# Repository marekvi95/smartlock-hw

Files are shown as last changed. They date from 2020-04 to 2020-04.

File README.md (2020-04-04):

# smartlock-hw

This repository contains PCB design for the **smartlock**. This project started as the final thesis at the Brno University of Technology. The aim of this project is to create a smartlock that that could be used for securing the objects.

Project is created with KiCAD version 6.0.0 nightly builds. KiCAD can be downloaded here https://kicad-pcb.org/download/

## Smartlock

Battery powered smartlock using IoT networks and NFC technology for the user authentication. Firmware source code is in this repo: https://github.com/marekvi95/smartlock-fw

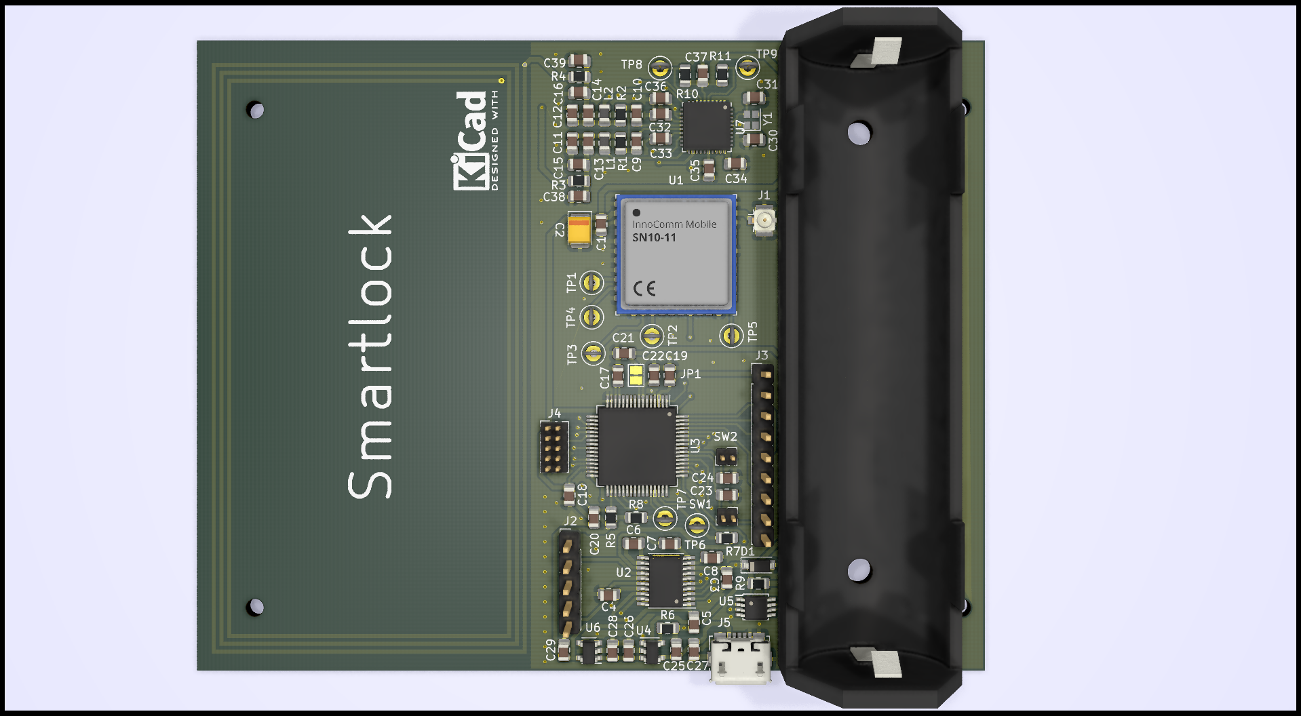
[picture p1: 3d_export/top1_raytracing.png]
Smartlock top


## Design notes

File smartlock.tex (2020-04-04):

\documentclass[a4paper]{article}
\usepackage[3D]{movie15}
\usepackage{hyperref}
\usepackage[UKenglish]{babel}
\begin{document}
\includemovie[
	poster,
	toolbar, %same as `controls'
	label=smartlock.u3d,
	text=(smartlock.u3d),
	3Daac=60.000000, 3Droll=0.000000, 3Dc2c=-0.143000 -0.139399 0.097560, 3Droo=0.222259, 3Dcoo=-0.143000 0.008699 -0.097555,
	3Dlights=CAD,
]{\linewidth}{\linewidth}{smartlock.u3d}
\end{document}

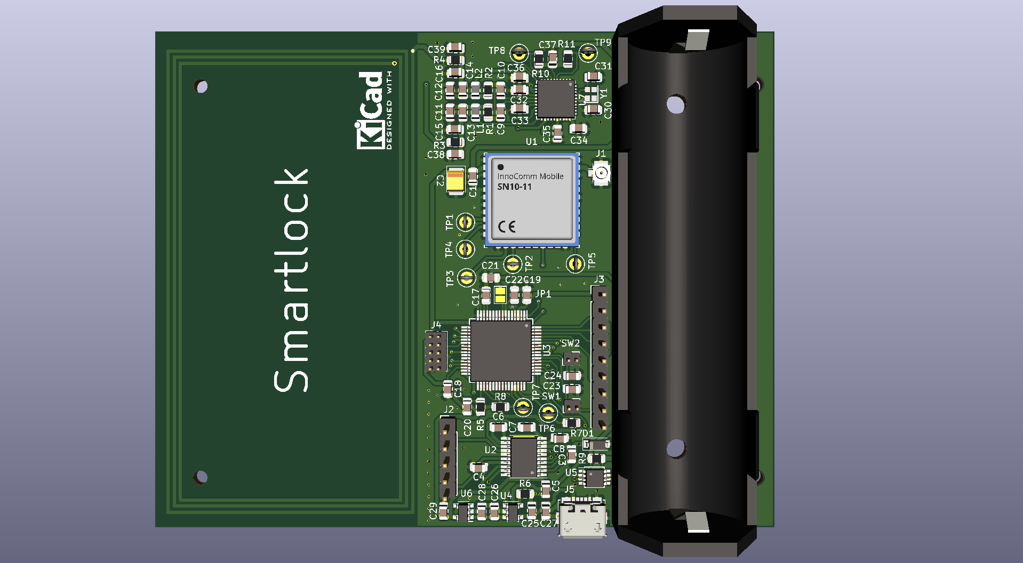
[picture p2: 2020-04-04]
3d_export/top1.png

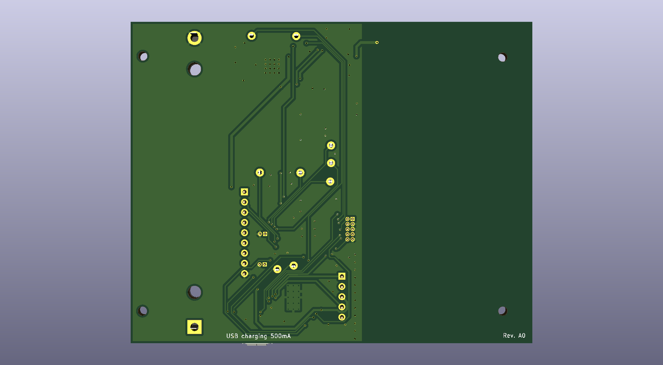
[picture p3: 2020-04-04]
3d_export/bottom1.png

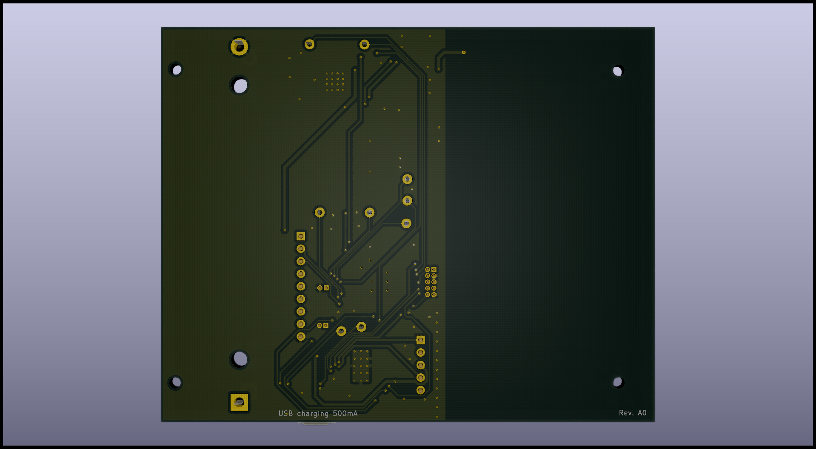
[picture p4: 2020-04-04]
3d_export/bottom1_raytracing.png

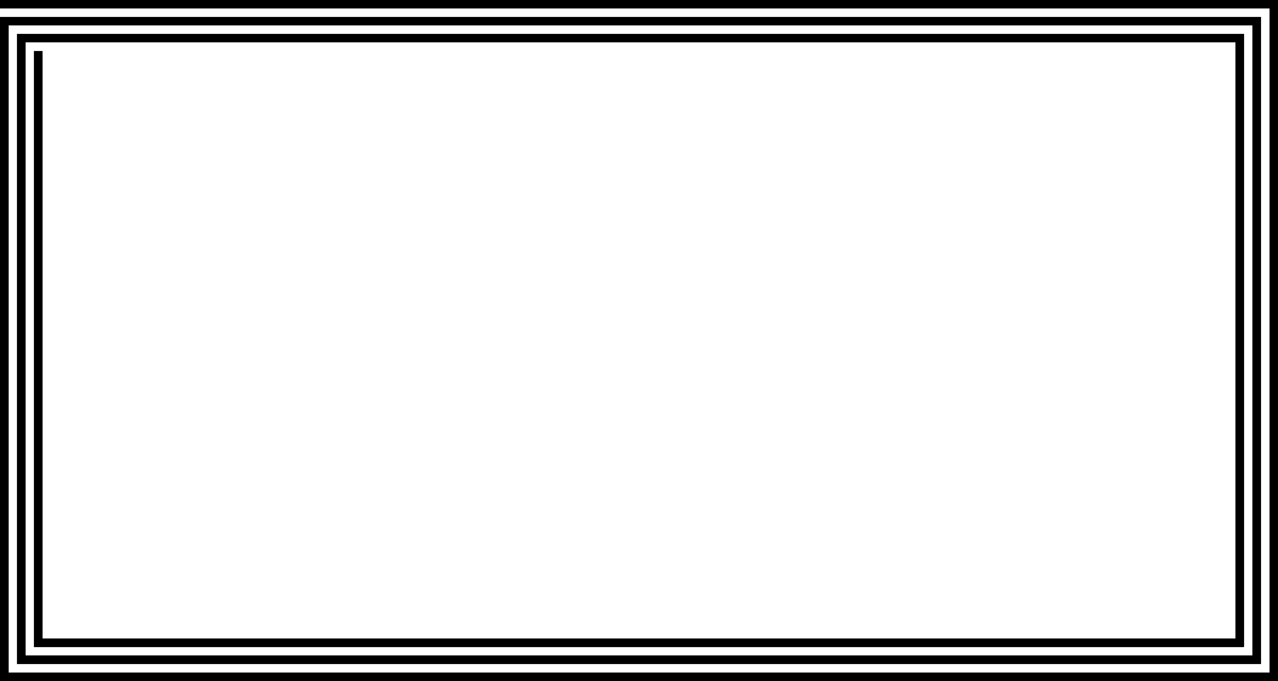
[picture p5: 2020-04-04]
antenna/antenna_40_75.png

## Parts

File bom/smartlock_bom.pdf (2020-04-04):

### Prj: Smartlock Co.: Marek Vitula Prj date: 12/14/2019 8:41:50 PM $ date: 2019-12-14 20:49:52

Refs | Value | Footprint
AE2 | Antenna Sigfox | Antenna:sigfox
BT1 | Battery_Cell | Battery:BatteryHolder_MPD_BH-18650-PC2
C1 | 33p | Capacitor_SMD:C_0805_2012Metric
C11,C12 | 250p/16V | Capacitor_SMD:C_0805_2012Metric
C13,C14 | 30p/50V | Capacitor_SMD:C_0805_2012Metric
C15,C16 | 150p/50V | Capacitor_SMD:C_0805_2012Metric
C2 | 47u/10V | Capacitor_Tantalum_SMD:CP_EIA-3528-21_Kemet-B
C28,C32-C34,C37 | 1u | Capacitor_SMD:C_0805_2012Metric
C3,C4,C25-C27,C36 | 4.7u | Capacitor_SMD:C_0805_2012Metric
C30,C31 | 10pF | Capacitor_SMD:C_0805_2012Metric
C38,C39 | 5p/50V | Capacitor_SMD:C_0805_2012Metric
C5,C21,C22,C29 | 2.2u | Capacitor_SMD:C_0805_2012Metric
C9,C10 | 1n | Capacitor_SMD:C_0805_2012Metric
C6-C8,C17-C20,C23,C24,C35 | 100n | Capacitor_SMD:C_0805_2012Metric
D1 | MMSZ5237BT1G | Diode_SMD:D_SOD-123
J1 | Hirose U.FL | Connector_Coaxial:U.FL_Hirose_U.FL-R-SMT-1_Vertical
J2 | Conn_01x05 | Connector_PinHeader_2.54mm:PinHeader_1x05_P2.54mm_Vertical
J3 | Conn_01x09 | Connector_PinHeader_2.54mm:PinHeader_1x09_P2.54mm_Vertical
J4 | Conn_ARM_JTAG_SWD_10 | Connector_PinHeader_1.27mm:PinHeader_2x05_P1.27mm_Vertical
J5 | USB_B_Micro | Connector_USB:USB_Micro-B_Molex_47346-0001
L1,L2 | 470n | Inductor_SMD:L_0805_2012Metric
R1,R2 | 1k | Resistor_SMD:R_0805_2012Metric
R3,R4 | 2.4R | Resistor_SMD:R_0805_2012Metric
R5 | 10k | Resistor_SMD:R_0805_2012Metric
R6 | 2k | Resistor_SMD:R_0805_2012Metric
R7,R8,R10,R11 | 4k7 | Resistor_SMD:R_0805_2012Metric
R9 | 10m | Resistor_SMD:R_0805_2012Metric
SW1,SW2 | SW_Push | Connector_PinHeader_1.27mm:PinHeader_1x02_P1.27mm_Vertical
U1 | INNOCOMM-SN10-11 | Antenna:InnoCommSN10-11
U2 | MPC17531ATEJ | Package_SO:HTSSOP-20-1EP_4.4x6.5mm_P0.65mm_EP3.4x6.5mm_ThermalVias
U3 | K32L2B21VLH0A | Package_QFP:LQFP-64_10x10mm_P0.5mm
U4 | MCP73831-2-OT | Package_TO_SOT_SMD:SOT-23-5
U5 | LTC2941CMS8E | Package_SO:MSOP-8-1EP_3x3mm_P0.65mm_EP1.68x1.88mm
U6 | TPS78330 | Package_TO_SOT_SMD:SOT-23-5
U7 | PN7150 | Package_DFN_QFN:QFN-40-1EP_6x6mm_P0.5mm_EP4.6x4.6mm
Y1 | XRCGB27M120F3M10R0 | Crystal:Crystal_SMD_2016-4Pin_2.0x1.6mm

# Global Part Info

Board Qty: | 3

### Unit Cost: CZK1,047.28 Total Cost: CZK3,141.85 CZK2,376.06 CZK1,504.56 CZK2,790.10 CZK924.34

Manf# | Qty | Unit$ | Ext$ | Ext$ | Ext$ | Ext$ | Ext$
206764-0100 | 3 | CZK62.45 | CZK187.36 | CZK250.18 | CZK187.36 | CZK250.18
1043 | 3 | CZK60.44 | CZK181.31 | CZK181.31 | CZK211.88 | CZK181.31
C0805C330K5HACAUTO | 3 | CZK0.52 | CZK1.56 | CZK1.56 | | CZK10.54
08055A251JAT2A | 6 | CZK6.79 | CZK40.76 | | | CZK40.76
08055A300GAT2A | 6 | CZK2.85 | CZK17.08 | CZK17.08 | | CZK66.06
08055A151FAT2A | 6 | CZK7.96 | CZK47.79 | CZK49.19 | CZK48.33 | CZK47.79
TPSB476M010T0250 | 3 | CZK8.15 | CZK24.46 | CZK24.46 | | CZK87.14
C0805C105K8RACTU | 15 | CZK1.08 | CZK16.16 | CZK62.55 | CZK25.04 | CZK16.16
C0805C475K8PACTU | 18 | CZK1.92 | CZK34.58 | CZK75.05 | CZK53.06 | CZK34.58
SQCFVA100JATME | 6 | CZK21.79 | CZK130.71 | CZK130.71 | | CZK130.71
08055A5R0CAT2A | 6 | CZK3.98 | CZK23.89 | CZK23.89 | | CZK23.89
C0805C225K8RACTU | 12 | CZK3.30 | CZK39.64 | CZK45.54 | CZK66.54 | CZK39.64
C0805C102J5GAC7210 | 6 | CZK3.05 | CZK18.27 | | | CZK18.27
C0805C104K8RACTU | 30 | CZK3.51 | CZK105.41 | CZK105.41 | CZK128.70 | CZK105.41
MMSZ5237BT1G | 3 | CZK4.69 | CZK14.06 | CZK14.06 | CZK14.36 | CZK14.06
U.FL-R-SMT-1(10) | 3 | CZK21.13 | CZK63.39 | CZK92.06 | CZK63.39 | CZK83.63
5-146274-5 | 3 | CZK5.50 | CZK16.50 | CZK16.50 | CZK40.97 | CZK26.00
22-30-3093 | 3 | CZK4.47 | CZK13.40 | CZK13.79 | CZK13.40 | CZK30.92
M50-3500542 (http://infocenter.arm.com/help/topic/com.arm.doc.ddi0314h/DDI0314H_coresight_components_trm.pdf) | 3 | CZK25.80 | CZK77.40 | CZK83.63 | CZK77.40 | CZK83.63
47346-0001 | 3 | CZK21.22 | CZK63.65 | CZK73.79 | CZK63.65 | CZK66.76
LQW21HNR47J00L | 6 | CZK11.71 | CZK70.28 | CZK70.28 | | CZK70.28
RT0805FRE071KL | 6 | CZK2.29 | CZK13.76 | CZK14.06 | CZK13.76 | CZK16.87
ESR10EZPF2R40 | 6 | CZK0.39 | CZK2.32 | CZK2.32 | | CZK22.49
RT0805FRE0710KL | 3 | CZK2.34 | CZK7.03 | CZK7.03 | CZK7.49 | CZK8.43
RT0805FRE072KL | 3 | CZK2.34 | CZK7.03 | CZK7.03 | | CZK8.43
RT0805FRE134K7L | 12 | CZK1.50 | CZK17.99 | | | CZK17.99
CFN0805-FX-R010ELF | 3 | CZK12.42 | CZK37.25 | CZK43.57 | | CZK37.25
M50-3530242 | 6 | CZK1.52 | CZK9.11 | CZK16.87 | CZK9.11 | CZK15.46
SN10-11-INNO | 10 | CZK92.43 | CZK924.34 | CZK924.34
MPC17531ATEJ (https://www.nxp.com/docs/en/data-sheet/MPC17531A.pdf) | 3 | CZK58.56 | CZK175.69 | CZK175.69 | CZK182.11 | CZK175.69
K32L2B21VLH0A | 3 | CZK69.43 | CZK208.30 | CZK208.30 | | CZK282.51
MCP73831T-3ACI/OT (http://ww1.microchip.com/downloads/en/DeviceDoc/20001984g.pdf) | 3 | CZK13.12 | CZK39.35 | CZK39.35 | CZK40.71 | CZK39.35
LTC2941CMS8E#PBF (http://cds.linear.com/docs/en/datasheet/2941fb.pdf) | 3 | CZK73.25 | CZK219.76 | CZK229.10 | CZK219.76 | CZK229.10
C0805C475K8PACTU (http://www.ti.com/lit/ds/symlink/tps783.pdf) | 3 | CZK2.95 | CZK8.84 | CZK18.27 | CZK8.84 | CZK11.95
PN7150B0HN/C11004Y (https://www.nxp.com/docs/en/data-sheet/PN7120.pdf) | 3 | CZK85.81 | CZK257.44 | CZK257.44 | | CZK470.85
XRCGB27M120F3M10R0 | 3 | CZK8.67 | CZK26.00 | CZK26.00 | CZK28.72 | CZK26.00
Digi-Key | Farnell | Mouser | Texim

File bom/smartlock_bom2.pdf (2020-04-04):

Prj: Smartlock
Co.: Marek Vitula
Prj date: 12/14/2019 8:41:50 PM $ date: 2019-12-14 20:49:52
Refs | Value
AE2 | Antenna Sigfox
BT1 | Battery_Cell
C1 | 33p
C11,C12 | 250p/16V
C13,C14 | 30p/50V
C15,C16 | 150p/50V
C2 | 47u/10V
C28,C32-C34,C37 1u
C3,C4,C25-C27,C36 4.7u
C30,C31 | 10pF
C38,C39 | 5p/50V
C5,C21,C22,C29 2.u
C9,C10 1n
C6-C8,C17-C20,C23,C24,C35 100n
D1 | MMSZ5237BT1G
J1 | Hirose U.FL
J2 | Conn_01x05
J3 | Conn_01x09
J4 | Conn_ARM_JTAG_SWD_10
J5 | USB_B_Micro
L1,L2 | 470n
R1,R2 | 1k
R3,R4 | 2.4R
R5 | 10k
R6 | 2k
R7,R8,R10,R11 4k7
R9 | 10m
SW1,SW2 SW_Push
U1 | INNOCOMM-SN10-11
U2 | MPC17531ATEJ
U3 | K32L2B21VLH0A
U4 | MCP73831-2-OT
U5 | LTC2941CMS8E
U6 | TPS78330
U7 | PN7150
Y1 | 27.12 MHz XRCGB27M120F3M10R0

Footprint

Antenna:sigfox
Battery:BatteryHolder_MPD_BH-18650-PC2 Capacitor_SMD:C_0805_2012Metric Capacitor_SMD:C_0805_2012Metric Capacitor_SMD:C_0805_2012Metric Capacitor_SMD:C_0805_2012Metric Capacitor_Tantalum_SMD:CP_EIA-3528-21_Kemet-B Capacitor_SMD:C_0805_2012Metric Capacitor_SMD:C_0805_2012Metric Capacitor_SMD:C_0805_2012Metric Capacitor_SMD:C_0805_2012Metric Capacitor_SMD:C_0805_2012Metric Capacitor_SMD:C_0805_2012Metric Capacitor_SMD:C_0805_2012Metric
Diode_SMD:D_SOD-123
Connector_Coaxial:U.FL_Hirose_U.FL-R-SMT-1_Vertical Connector_PinHeader_2.54mm:PinHeader_1x05_P2.54mm_Vertical Connector_PinHeader_2.54mm:PinHeader_1x09_P2.54mm_Vertical Connector_PinHeader_1.27mm:PinHeader_2x05_P1.27mm_Vertical Connector_USB:USB_Micro-B_Molex_47346-0001 Inductor_SMD:L_0805_2012Metric Resistor_SMD:R_0805_2012Metric Resistor_SMD:R_0805_2012Metric Resistor_SMD:R_0805_2012Metric Resistor_SMD:R_0805_2012Metric Resistor_SMD:R_0805_2012Metric Resistor_SMD:R_0805_2012Metric Connector_PinHeader_1.27mm:PinHeader_1x02_P1.27mm_Vertical Antenna:InnoCommSN10-11
Package_SO:HTSSOP-20-1EP_4.4x6.5mm_P0.65mm_EP3.4x6.5mm_ThermalVias Package_QFP:LQFP-64_10x10mm_P0.5mm
Package_TO_SOT_SMD:SOT-23-5 Package_SO:MSOP-8-1EP_3x3mm_P0.65mm_EP1.68x1.88mm Package_TO_SOT_SMD:SOT-23-5 Package_DFN_QFN:QFN-40-1EP_6x6mm_P0.5mm_EP4.6x4.6mm Crystal:Crystal_SMD_2016-4Pin_2.0x1.6mm

### Global Part Info

Board Qty: | 3
Unit Cost: | CZK1,047.28
Total Cost: | CZK3,141.85 | CZK2,376.06 | CZK1,504.56
Manf# | Qty | Unit$ | Ext$ | Ext$ | Ext$
206764-0100 | 3 | CZK62.45 | CZK187.36 | CZK250.18 | CZK187.36
1043 | 3 | CZK60.44 | CZK181.31 | CZK181.31 | CZK211.88
C0805C330K5HACAUTO | 3 | CZK0.52 | CZK1.56 | CZK1.56
08055A251JAT2A | 6 | CZK6.79 | CZK40.76
08055A300GAT2A | 6 | CZK2.85 | CZK17.08 | CZK17.08
08055A151FAT2A | 6 | CZK7.96 | CZK47.79 | CZK49.19 | CZK48.33
TPSB476M010T0250 | 3 | CZK8.15 | CZK24.46 | CZK24.46
C0805C105K8RACTU | 15 | CZK1.08 | CZK16.16 | CZK62.55 | CZK25.04
C0805C475K8PACTU | 18 | CZK1.92 | CZK34.58 | CZK75.05 | CZK53.06
SQCFVA100JATME | 6 | CZK21.79 | CZK130.71 | CZK130.71
08055A5R0CAT2A | 6 | CZK3.98 | CZK23.89 | CZK23.89
C0805C225K8RACTU | 12 | CZK3.30 | CZK39.64 | CZK45.54 | CZK66.54
C0805C102J5GAC7210 | 6 | CZK3.05 | CZK18.27
C0805C104K8RACTU | 30 | CZK3.51 | CZK105.41 | CZK105.41 | CZK128.70
MMSZ5237BT1G | 3 | CZK4.69 | CZK14.06 | CZK14.06 | CZK14.36
U.FL-R-SMT-1(10) | 3 | CZK21.13 | CZK63.39 | CZK92.06 | CZK63.39
5-146274-5 | 3 | CZK5.50 | CZK16.50 | CZK16.50 | CZK40.97
22-30-3093 | 3 | CZK4.47 | CZK13.40 | CZK13.79 | CZK13.40
M50-3500542 (http://infocenter.arm.com/help/topic/com.arm.doc.ddi0314h/DDI0314H_coresight_components_trm.pdf) | 3 | CZK25.80 | CZK77.40 | CZK83.63 | CZK77.40
47346-0001 | 3 | CZK21.22 | CZK63.65 | CZK73.79 | CZK63.65
LQW21HNR47J00L | 6 | CZK11.71 | CZK70.28 | CZK70.28
RT0805FRE071KL | 6 | CZK2.29 | CZK13.76 | CZK14.06 | CZK13.76
ESR10EZPF2R40 | 6 | CZK0.39 | CZK2.32 | CZK2.32
RT0805FRE0710KL | 3 | CZK2.34 | CZK7.03 | CZK7.03 | CZK7.49
RT0805FRE072KL | 3 | CZK2.34 | CZK7.03 | CZK7.03
RT0805FRE134K7L | 12 | CZK1.50 | CZK17.99
CFN0805-FX-R010ELF | 3 | CZK12.42 | CZK37.25 | CZK43.57
M50-3530242 | 6 | CZK1.52 | CZK9.11 | CZK16.87 | CZK9.11
SN10-11-INNO | 10 | CZK92.43 | CZK924.34
MPC17531ATEJ (https://www.nxp.com/docs/en/data-sheet/MPC17531A.pdf) | 3 | CZK58.56 | CZK175.69 | CZK175.69 | CZK182.11
K32L2B21VLH0A | 3 | CZK69.43 | CZK208.30 | CZK208.30
MCP73831T-3ACI/OT (http://ww1.microchip.com/downloads/en/DeviceDoc/20001984g.pdf) | 3 | CZK13.12 | CZK39.35 | CZK39.35 | CZK40.71
LTC2941CMS8E#PBF (http://cds.linear.com/docs/en/datasheet/2941fb.pdf) | 3 | CZK73.25 | CZK219.76 | CZK229.10 | CZK219.76
C0805C475K8PACTU (http://www.ti.com/lit/ds/symlink/tps783.pdf) | 3 | CZK2.95 | CZK8.84 | CZK18.27 | CZK8.84
PN7150B0HN/C11004Y (https://www.nxp.com/docs/en/data-sheet/PN7120.pdf) | 3 | CZK85.81 | CZK257.44 | CZK257.44
XRCGB27M120F3M10R0 | 3 | CZK8.67 | CZK26.00 | CZK26.00 | CZK28.72
Digi-Key | Farnell

CZK2,790.10 | CZK924.34
Ext$ | Ext$

CZK250.18
CZK181.31
CZK10.54
CZK40.76
CZK66.06
CZK47.79
CZK87.14
CZK16.16
CZK34.58
CZK130.71
CZK23.89
CZK39.64
CZK18.27
CZK105.41
CZK14.06
CZK83.63
CZK26.00
CZK30.92
CZK83.63
CZK66.76
CZK70.28
CZK16.87
CZK22.49
CZK8.43
CZK8.43
CZK17.99
CZK37.25
CZK15.46
| CZK924.34
CZK175.69
CZK282.51
CZK39.35
CZK229.10
CZK11.95
CZK470.85
CZK26.00
Mouser | Texim

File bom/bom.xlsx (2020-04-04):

Source: | C:\Users\nxf46245\Documents\github\diplomka\schema.sch
Date: | 2019-12-08 17:12
Tool: | Eeschema (5.1.2)-1
Generator: | C:\Program Files\KiCad\bin\scripting\plugins/bom_csv_grouped_by_value_with_fp.py |  |  |  |  |  | Part number | URL | Cena | Nazev | Vyribce
Component Count: | 78
Ref | Qnty | Value | Cmp name | Footprint | Description | Vendor
AE1, | 1 | Antenna | Antenna_Loop | Antenna:nfc_40_75 | Loop antenna
BT1, | 1 | Battery_Cell | Battery_Cell | Battery:BatteryHolder_MPD_BH-18650-PC2 | Single-cell battery |  | BK-18650-PC2 | https://www.digikey.com/product-detail/en/mpd-memory-protection-devices/BK-18650-PC2/BK-18650-PC2-ND/2079908 | 70 |  | Memory protection devices
C1, | 1 | 33p | C | Capacitor_SMD:C_0805_2012Metric | Unpolarized capacitor |  | C0805C330K5HACAUTO (https://cz.mouser.com/ProductDetail/KEMET/C0805C330K5HACAUTO) |  | 3,51 |  | Kemet
C2, | 1 | 47u 10V | CP | Capacitor_Tantalum_SMD:CP_EIA-3528-21_Kemet-B | Polarized capacitor |  | TPSB476M010T0250 (https://cz.mouser.com/ProductDetail/AVX/TPSB476M010T0250)
C4, C3, C27, C25, C26, | 5 | 4.7u | C | Capacitor_SMD:C_0805_2012Metric | Unpolarized capacitor |  | C0805C475K8PACTU (https://cz.mouser.com/ProductDetail/KEMET/C0805C475K3RACAUTO) |  | 3,98 |  | KEMET | Vícevrstvé keramické kondenzátory MLCC – pro povrchovou montáž SMD, SMT 4.7UF 10V 10% 0805
C5, C22, C21, C29, | 4 | 2.2u | C | Capacitor_SMD:C_0805_2012Metric | Unpolarized capacitor |  | C0805C225K8RACTU (https://cz.mouser.com/ProductDetail/KEMET/C0805C225K8RACTU) |  | 3,74 |  | KEMET | Vícevrstvé keramické kondenzátory MLCC – pro povrchovou montáž SMD, SMT 2.2UF 10V 10% 0805
C7, C8, C6, C17, C18, C19, C20, C24, C23, C35, | 10 | 100n | C | Capacitor_SMD:C_0805_2012Metric | Unpolarized capacitor |  | C0805C104K8RACTU |  | 4,91 |  | KEMET | Vícevrstvé keramické kondenzátory MLCC – pro povrchovou montáž SMD, SMT 10V 0.1uF X7R 0805 10%
C10, C9, | 2 | 1nF | C | Capacitor_SMD:C_0805_2012Metric | Unpolarized capacitor |  | C0805C102J5GAC7210 (https://cz.mouser.com/ProductDetail/KEMET/C0805C102J5GAC7210) |  | 3,04 |  | KEMET | Vícevrstvé keramické kondenzátory MLCC – pro povrchovou montáž SMD, SMT 50V 1000pF C0G 0805 5%
C11, C12, | 2 | 250pF/16V | C | Capacitor_SMD:C_0805_2012Metric | Unpolarized capacitor |  | 08055A251JAT2A (https://cz.mouser.com/ProductDetail/AVX/08055A251JAT2A?qs=sGAEpiMZZMs0AnBnWHyRQO2a6rsPNabdznzp3AE1pn4%3D) |  | 6.79 |  | AVX | Vícevrstvé keramické kondenzátory MLCC – pro povrchovou montáž SMD, SMT 50V 250pF C0G 0805 5% To
C13, C14, | 2 | 30p/50V | C | Capacitor_SMD:C_0805_2012Metric | Unpolarized capacitor |  | 08055A300GAT2A (https://cz.mouser.com/ProductDetail/AVX/08055A300GAT2A?qs=sGAEpiMZZMs0AnBnWHyRQO2a6rsPNabdEripVQmQLXA%3D) |  | 11 |  | AVX | Vícevrstvé keramické kondenzátory MLCC – pro povrchovou montáž SMD, SMT 50V 30 pF 0.02 2% Tol
C15, C16, | 2 | 155pF/50V | C | Capacitor_SMD:C_0805_2012Metric | Unpolarized capacitor |  | 08055A151FAT2A (https://cz.mouser.com/ProductDetail/AVX/08055A151FAT2A) |  | 7.96 |  | AVX
C28, | 1 | 1u | C | Capacitor_SMD:C_0805_2012Metric | Unpolarized capacitor |  | C0805C105K8RACTU (https://cz.mouser.com/ProductDetail/KEMET/C0805C105K8RACTU?qs=sGAEpiMZZMs0AnBnWHyRQOf5HOpVaXbhbdNkQWski8Q%3D) |  | 2,57 |  | KEMET
C30, C31, | 2 | 10pF | C | Capacitor_SMD:C_0805_2012Metric | Unpolarized capacitor |  | SQCFVA100JATME (https://cz.mouser.com/ProductDetail/AVX/SQCFVA100JATME) |  | 21,76 |  | AVX | Vícevrstvé keramické kondenzátory MLCC – pro povrchovou montáž SMD, SMT 250V 10pF 0805 0+-30ppm/oC 5% Tol
C34, C37, C33, C32, | 4 | 1uF | C | Capacitor_SMD:C_0805_2012Metric | Unpolarized capacitor |  | C0805C105K8RACTU (https://cz.mouser.com/ProductDetail/KEMET/C0805C105K8RACTU?qs=sGAEpiMZZMs0AnBnWHyRQOf5HOpVaXbhbdNkQWski8Q%3D) |  | 2,57 |  | KEMET | Vícevrstvé keramické kondenzátory MLCC – pro povrchovou montáž SMD, SMT 10V 1uF X7R 0805 10%
C36, | 1 | 4.7uF | C | Capacitor_SMD:C_0805_2012Metric | Unpolarized capacitor |  | C0805C475K8PACTU |  | 3,98 |  | KEMET | Vícevrstvé keramické kondenzátory MLCC – pro povrchovou montáž SMD, SMT 4.7UF 10V 10% 0805
D1, | 1 | MMSZ5237BT1G | D_Zener | Diode_SMD:D_SOD-123 | Zener diode |  | MMSZ5237BT1G (https://cz.mouser.com/ProductDetail/ON-Semiconductor/MMSZ5237BT1G) |  | 4,68 |  | ON Semiconductor | Zenerovy diody 8.2V 500mW
J1, | 1 | Conn_Coaxial | Conn_Coaxial | Connector_Coaxial:U.FL_Hirose_U.FL-R-SMT-1_Vertical | coaxial connector (BNC, SMA, SMB, SMC, Cinch/RCA, ...) |  | U.FL-R-SMT-1(10) (https://cz.mouser.com/ProductDetail/Hirose-Connector/UFL-R-SMT-110?qs=sGAEpiMZZMtJvlLX7mFQSOnc7FkNSTvj) |  | 27,82 |  | Hirose connector | VF koaxiální konektory SMT ML REC AU 50 OHM W/ANTI SLDR WCKNG RL
J2, | 1 | Conn_01x05 | Conn_01x05 | Connector_PinHeader_2.54mm:PinHeader_1x05_P2.54mm_Vertical | Generic connector, single row, 01x05, script generated (kicad-library-utils/schlib/autogen/connector/)
J3, | 1 | Conn_01x09 | Conn_01x09 | Connector_PinHeader_2.54mm:PinHeader_1x09_P2.54mm_Vertical | Generic connector, single row, 01x09, script generated (kicad-library-utils/schlib/autogen/connector/)
J4, | 1 | Conn_ARM_JTAG_SWD_10 | Conn_ARM_JTAG_SWD_10 | Connector_PinHeader_1.27mm:PinHeader_2x05_P1.27mm_Vertical | Cortex Debug Connector, standard ARM Cortex-M SWD and JTAG interface
J5, | 1 | USB_B_Micro | USB_B_Micro | Connector_USB:USB_Micro-B_Molex_47346-0001 | USB Micro Type B connector
JP1, | 1 | Jumper | Jumper | Jumper:SolderJumper-2_P1.3mm_Bridged_Pad1.0x1.5mm | Jumper, normally closed
L1, L2, | 2 | 470n | L | Inductor_SMD:L_0805_2012Metric | Inductor |  | LQM21NNR47K10D (https://cz.mouser.com/ProductDetail/Murata-Electronics/LQM21NNR47K10D) |  | 5,15 Kč |  | Murata | Pevné cívky 0805 0.47uH 10%
R1, R2, | 2 | 1k | R | Resistor_SMD:R_0805_2012Metric | Resistor |  | RT0805FRE101KL (https://cz.mouser.com/ProductDetail/Yageo/RT0805FRE101KL) |  | 2,81 |  | Yageo | Tenkovrstvé rezistory - SMD 1K ohm 1% 50 ppm Thin Film
R3, R4, | 2 | 2 | R | Resistor_SMD:R_0805_2012Metric | Resistor
R5, | 1 | 10k | R | Resistor_SMD:R_0805_2012Metric | Resistor
R6, | 1 | 2k | R | Resistor_SMD:R_0805_2012Metric | Resistor |  | RT0805FRE072KL (https://cz.mouser.com/ProductDetail/Yageo/RT0805FRE072KL?qs=sGAEpiMZZMu61qfTUdNhG17bj55vCpcBFqPDyz80noY%3D) |  | 2,81 |  | Yageo | Tenkovrstvé rezistory - SMD 1/8W 2K ohm 1% 50ppm
R8, R7, R10, R11, | 4 | 4k7 | R | Resistor_SMD:R_0805_2012Metric | Resistor |  | RT0805FRE134K7L (https://cz.mouser.com/ProductDetail/Yageo/RT0805FRE134K7L) |  | 2,81 |  | Yageo | https://cz.mouser.com/manufacturer/yageo/ | Tenkovrstvé rezistory - SMD 4.7K ohm 1% 50 ppm Thin Film
R9, | 1 | 10m | R | Resistor_SMD:R_0805_2012Metric | Resistor |  | TLR2BDTD12L0F75 |  | 16,48 |  | KOA | Rezistory ke snímání proudu - SMD 2W 12 mOhm 1%
SW1, SW2, | 2 | SW_Push | SW_Push | Connector_PinHeader_1.27mm:PinHeader_1x02_P1.27mm_Vertical | Push button switch, generic, two pins
TP1, | 1 | SDI1_TP | TestPoint | TestPoint:TestPoint_Loop_D2.50mm_Drill1.0mm_LowProfile | test point
TP2, | 1 | SDO1_TP | TestPoint | TestPoint:TestPoint_Loop_D2.50mm_Drill1.0mm_LowProfile | test point
TP3, | 1 | SCLK1_TP | TestPoint | TestPoint:TestPoint_Loop_D2.50mm_Drill1.0mm_LowProfile | test point
TP4, | 1 | CS1_TP | TestPoint | TestPoint:TestPoint_Loop_D2.50mm_Drill1.0mm_LowProfile | test point
TP5, | 1 | AK1_TP | TestPoint | TestPoint:TestPoint_Loop_D2.50mm_Drill1.0mm_LowProfile | test point
TP6, TP9, | 2 | I2C_D2_TP | TestPoint | TestPoint:TestPoint_Loop_D2.50mm_Drill1.0mm_LowProfile | test point
TP7, | 1 | I2C_C2_TP | TestPoint | TestPoint:TestPoint_Loop_D2.50mm_Drill1.0mm_LowProfile | test point
TP8, | 1 | I2C_C1_TP | TestPoint | TestPoint:TestPoint_Loop_D2.50mm_Drill1.0mm_LowProfile | test point
U1, | 1 | INNOCOMM-SN10-11 | INNOCOMM-SN10-11 | Antenna:InnoCommSN10-11 | InnoComm SN10-11 Sigfox module
U2, | 1 | MPC17531ATEJ | MPC17531ATEJ | Package_SO:HTSSOP-20-1EP_4.4x6.5mm_P0.65mm_EP3.4x6.5mm_ThermalVias | 700 mA dual H-Bridge motor driver with 3.0 V compatible logic I/O |  | MPC17531ATEJ (https://cz.mouser.com/ProductDetail/NXP-Semiconductors/MPC17531ATEJ) |  | 58,50 |  | NXP | Motorové / Pohyblivé / Zážehové ovladače a mechanismy H-Bridge, Dual, Low Voltage, Stepper & DC Brushed Motor Driver, 2-8.6V, 1.4A, 200kHz, TSSOP-EP
U3, | 1 | K32L2B21VLH0A | K32L2B21VLH0A | Package_QFP:LQFP-64_10x10mm_P0.5mm | Kinetis KL32L2B series, 48-MHz/32-bit ARM Cortex-M0+, 128kB flash, 32 kB SRAM, USB FS Device (xtal-less), Segment LCD, FlexIO, LQFP-64 |  | K32L2B21VLH0A |  | 94,12 |  | NXP | Mikrořadiče ARM – MCU K32 L2B, 64LQFP
U4, | 1 | MCP73831-2-OT | MCP73831-2-OT | Package_TO_SOT_SMD:SOT-23-5 | Single cell, Li-Ion/Li-Po charge management controller, 4.20V, Tri-State Status Output, in SOT23-5 package |  | MCP73831T-3ACI/OT (https://cz.mouser.com/ProductDetail/Microchip-Technology/MCP73831T-3ACI-OT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) |  | 13,10 |  | Microchip | Řízení baterie Charge mgnt contr
U5, | 1 | LTC2941CMS8E | LTC2941CMS8E | Package_SO:MSOP-8-1EP_3x3mm_P0.65mm_EP1.68x1.88mm | Battery Gas Gauge with I2C Interface |  | LTC2941CMS8E#PBF (https://cz.mouser.com/ProductDetail/Analog-Devices-Linear-Technology/LTC2941CMS8EPBF) |  | 76,18 |  | Analog Devices | Řízení baterie Battery Gas Gauge w/ I2C
U6, | 1 | TPS78330 | TPS78330 | Package_TO_SOT_SMD:SOT-23-5 | Ultralow Quiescent Current 150mA LDO, 3.0V fixed output voltage, SOT-23-5 |  | TPS78330DDCR (https://cz.mouser.com/ProductDetail/Texas-Instruments/TPS78330DDCR) |  | 21,29 |  | TI | Regulátory napětí s nízkým úbytkem (LDO) 150mA Ultra-Lo Quies Crnt Iq0.5uA LDO Reg
U7, | 1 | PN7150 | PN7150 | Package_DFN_QFN:QFN-40-1EP_6x6mm_P0.5mm_EP4.6x4.6mm_ThermalVias | PN7120 - Full NFC Forum-compliant controller with integrated firmware and NCI interface |  | PN7150B0HN/C11004Y (https://cz.mouser.com/ProductDetail/NXP-Semiconductors/PN7150B0HN-C11004Y) |  | 156,78 |  | NXP | Transpondéry RFID High performance NFC controller, supporting all NFC Forum modes, with integrated firmware and NCI interface.
Y1, | 1 | 27.12 MHz XRCGB27M120F3M10R0 | Crystal_GND24 | Crystal:Crystal_SMD_2016-4Pin_2.0x1.6mm | Four pin crystal, GND on pins 2 and 4

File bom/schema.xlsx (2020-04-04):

Prj: | Smartlock |  |  |  | Board Qty: | 3
Co.: | Marek Vitula |  |  |  | Unit Cost: | CZK 561.02
Prj date: | 12/9/2019 9:29:18 PM |  |  |  | Total Cost: | CZK 1683.06 |  |  |  | CZK 2074.48 | 0 |  |  |  | CZK 1090.69 | 0 |  |  |  | CZK 2263.73 | 0 |  |  |  | CZK 1451.06 | 0 |  |  |  | CZK 127649.02 | 0
$ date: | 2019-12-09 21:32:31
Global Part Info |  |  |  |  |  |  | Digi-Key |  |  |  |  | Farnell |  |  |  |  | Mouser |  |  |  |  | Newark |  |  |  |  | Rs Components
Refs | Value | Footprint | Manf# | Qty | Unit$ | Ext$ | Avail | Purch | Unit$ | Ext$ | Cat# | Avail | Purch | Unit$ | Ext$ | Cat# | Avail | Purch | Unit$ | Ext$ | Cat# | Avail | Purch | Unit$ | Ext$ | Cat# | Avail | Purch | Unit$ | Ext$ | Cat#
AE1 | Antenna | Antenna:nfc_40_75 |  | 3 | CZK 0.00 | CZK 0.00
BT1 | Battery_Cell | Battery:BatteryHolder_MPD_BH-18650-PC2 | BK-18650-PC2 | 3 | CZK 78.01 | CZK 234.02 | 2094 |  | CZK 78.01 | CZK 234.02 | BK-18650-PC2-ND (https://octopart.com/click/track?c=1&ai=8078&sig=0df057f&sid=459&ppid=10598814&vpid=33662670&ct=offers)
C1 | 33p | Capacitor_SMD:C_0805_2012Metric | C0805C330K5HACAUTO | 3 | CZK 0.52 | CZK 1.56 | NonStk |  | CZK 0.52 | CZK 1.56 | C0805C330K5HACAUTO-ND (https://octopart.com/click/track?c=1&ai=8078&sig=0fb1fde&sid=459&ppid=88095168&vpid=456007969&ct=offers) |  |  |  |  |  | 11408 |  | CZK 3.51 | CZK 10.54 | 80C0805C330K5HAUTO (https://octopart.com/click/track?ai=8078&sig=0177dc9&sid=2401&ppid=88095168&vpid=458161513&ct=offers)
C11,C12 | 250p/16V | Capacitor_SMD:C_0805_2012Metric | 08055A251JAT2A | 6 | CZK 6.79 | CZK 40.76 | NonStk |  |  |  | 08055A251JAT2A-ND (https://octopart.com/click/track?c=1&ai=8078&sig=090d1b3&sid=459&ppid=8665191&vpid=33541788&ct=offers) |  |  |  |  |  | 18712 |  | CZK 6.79 | CZK 40.76 | 58108055A251JAT2A (https://octopart.com/click/track?ai=8078&sig=033ec15&sid=2401&ppid=8665191&vpid=457557647&ct=offers)
C13,C14 | 30p/50V | Capacitor_SMD:C_0805_2012Metric | 08055A300GAT2A | 6 | CZK 2.85 | CZK 17.08 | NonStk |  | CZK 2.85 | CZK 17.08 | 08055A300GAT2A-ND (https://octopart.com/click/track?c=1&ai=8078&sig=0358c8e&sid=459&ppid=9080631&vpid=33541825&ct=offers) |  |  |  |  |  | 275 |  | CZK 11.01 | CZK 66.06 | 58108055A300GAT2A (https://octopart.com/click/track?ai=8078&sig=071dcd3&sid=2401&ppid=9080631&vpid=456348598&ct=offers)
C15,C16 | 150p/50V | Capacitor_SMD:C_0805_2012Metric | 08055A151FAT2A | 6 | CZK 1.34 | CZK 8.01 | 61070 |  | CZK 8.20 | CZK 49.19 | 478-6219-6-ND (https://octopart.com/click/track?ai=8078&sig=09822c0&sid=459&ppid=2337672&vpid=34028323&ct=offers) | 16000 |  | CZK 8.05 | CZK 48.33 | 2918696 (https://octopart.com/click/track?ai=8078&sig=059797a&sid=819&ppid=2337672&vpid=500011276&ct=offers) | 25794 |  | CZK 7.96 | CZK 47.79 | 58108055A151FAT2A (https://octopart.com/click/track?ai=8078&sig=0ee936d&sid=2401&ppid=2337672&vpid=44735610&ct=offers) | 16000 |  | CZK 1.34 | CZK 8.01 | 96Y8488 (https://octopart.com/click/track?ai=8078&sig=0d7a7d0&sid=2402&ppid=2337672&vpid=271948959&ct=offers) | 19600 |  | CZK 3.01 | CZK 18.04 | 1359034 (https://octopart.com/click/track?c=1&ai=8078&sig=01a8ddf&sid=10022&ppid=2337672&vpid=500984126&ct=offers)
C2 | 47u/10V | Capacitor_Tantalum_SMD:CP_EIA-3528-21_Kemet-B | TPSB476M010T0250 | 3 | CZK 8.15 | CZK 24.46 | NonStk |  | CZK 8.15 | CZK 24.46 | 478-TPSB476M010T0250TR-ND (https://octopart.com/click/track?c=1&ai=8078&sig=09a8646&sid=459&ppid=47029682&vpid=596809048&ct=offers) |  |  |  |  |  | 1782 |  | CZK 29.05 | CZK 87.14 | 581TPSB476M010T0250 (https://octopart.com/click/track?ai=8078&sig=00f6d83&sid=2401&ppid=47029682&vpid=330475144&ct=offers)
C28,C32-C34,C37 | 1u | Capacitor_SMD:C_0805_2012Metric | C0805C105K8RACTU | 15 | CZK 1.08 | CZK 16.16 | 251117 |  | CZK 4.17 | CZK 62.55 | 399-1172-6-ND (https://octopart.com/click/track?ai=8078&sig=0a9ccea&sid=459&ppid=103379&vpid=34044386&ct=offers) | 36000 |  | CZK 1.67 | CZK 25.04 | 2409048 (https://octopart.com/click/track?ai=8078&sig=0d0e397&sid=11744&ppid=103379&vpid=133110117&ct=offers) | 173571 |  | CZK 1.08 | CZK 16.16 | 80C0805C105K8R (https://octopart.com/click/track?ai=8078&sig=09c9d55&sid=2401&ppid=103379&vpid=44736975&ct=offers) | 20000 |  | CZK 6.58 | CZK 98.74 | 64K2894 (https://octopart.com/click/track?ai=8078&sig=05fac39&sid=2402&ppid=103379&vpid=16452352&ct=offers) | 27000 |  | CZK 1.08 | CZK 16.20 | 8692149 (https://octopart.com/click/track?c=1&ai=8078&sig=03b1c91&sid=10022&ppid=103379&vpid=562613324&ct=offers)
C3,C4,C25-C27,C36 | 4.7u | Capacitor_SMD:C_0805_2012Metric | C0805C475K8PACTU | 18 | CZK 1.92 | CZK 34.58 | 243099 |  | CZK 4.17 | CZK 75.05 | 399-3133-1-ND (https://octopart.com/click/track?ai=8078&sig=006f170&sid=459&ppid=107582&vpid=1698235&ct=offers) | 217500 |  | CZK 2.95 | CZK 53.06 | 2409055 (https://octopart.com/click/track?ai=8078&sig=09b40ce&sid=819&ppid=107582&vpid=138967804&ct=offers) | 70384 |  | CZK 1.92 | CZK 34.58 | 80C0805C475K8P (https://octopart.com/click/track?ai=8078&sig=0d66b76&sid=2401&ppid=107582&vpid=44737003&ct=offers) | 35000 |  | CZK 6.00 | CZK 107.94 | 70K9144 (https://octopart.com/click/track?ai=8078&sig=08b9cc6&sid=2402&ppid=107582&vpid=16452459&ct=offers) | 32150 |  | CZK 1.93 | CZK 34.67 | 4516284 (https://octopart.com/click/track?ai=8078&sig=09077a8&sid=10022&ppid=107582&vpid=199040127&ct=offers)
C30,C31 | 10pF | Capacitor_SMD:C_0805_2012Metric | SQCFVA100JATME | 6 | CZK 7.66 | CZK 45.96 | 2268 |  | CZK 21.79 | CZK 130.71 | 478-4080-1-ND (https://octopart.com/click/track?ai=8078&sig=005143c&sid=459&ppid=583822&vpid=1587422&ct=offers) |  |  |  |  |  | 903 |  | CZK 21.79 | CZK 130.71 | 581SQCFVA100JATME (https://octopart.com/click/track?ai=8078&sig=0f52578&sid=2401&ppid=583822&vpid=37763208&ct=offers) | NonStk |  | CZK 7.66 | CZK 45.96 | 65M2973 (https://octopart.com/click/track?c=1&ai=8078&sig=01a14ed&sid=2402&ppid=583822&vpid=13291465&ct=offers)
C5,C21,C22,C29 | 2.2u | Capacitor_SMD:C_0805_2012Metric | C0805C225K8RACTU | 12 | CZK 3.30 | CZK 39.64 | 717817 |  | CZK 3.79 | CZK 45.54 | 399-3522-1-ND (https://octopart.com/click/track?ai=8078&sig=0466712&sid=459&ppid=123103&vpid=1581545&ct=offers) | 200000 |  | CZK 5.54 | CZK 66.54 | 2429358 (https://octopart.com/click/track?ai=8078&sig=02beb32&sid=11744&ppid=123103&vpid=132343678&ct=offers) | 42160 |  | CZK 3.30 | CZK 39.64 | 80C0805C225K8R (https://octopart.com/click/track?ai=8078&sig=07dfb66&sid=2401&ppid=123103&vpid=37733072&ct=offers) | 5051 |  | CZK 4.92 | CZK 59.03 | 77R3564 (https://octopart.com/click/track?ai=8078&sig=089d027&sid=2402&ppid=123103&vpid=23662386&ct=offers) | NonStk |  | CZK 2029.45 | CZK 24353.42 | 8695656 (https://octopart.com/click/track?c=1&ai=8078&sig=08312b0&sid=10022&ppid=123103&vpid=222592721&ct=offers)
C9,C10 | 1n | Capacitor_SMD:C_0805_2012Metric | C0805C102J5GAC7210 | 6 | CZK 3.05 | CZK 18.27 |  |  |  |  |  |  |  |  |  |  | 37762 |  | CZK 3.05 | CZK 18.27 | 80C0805C102J5G7210 (https://octopart.com/click/track?ai=8078&sig=04fd7d4&sid=2401&ppid=3919475&vpid=464250300&ct=offers)
C6-C8,C17-C20,C23,C24,C35 | 100n | Capacitor_SMD:C_0805_2012Metric | C0805C104K8RACTU | 30 | CZK 0.91 | CZK 27.41 | 90019 |  | CZK 3.51 | CZK 105.41 | 399-7999-6-ND (https://octopart.com/click/track?ai=8078&sig=023cb7d&sid=459&ppid=9139201&vpid=51926868&ct=offers) | 3945 |  | CZK 4.29 | CZK 128.70 | 2773207 (https://octopart.com/click/track?ai=8078&sig=0e9dbc7&sid=819&ppid=9139201&vpid=474066563&ct=offers) | 16586 |  | CZK 3.51 | CZK 105.41 | 80C0805C104K8R (https://octopart.com/click/track?ai=8078&sig=02448c2&sid=2401&ppid=9139201&vpid=37732175&ct=offers) | 8312 |  | CZK 0.91 | CZK 27.41 | 07X0869 (https://octopart.com/click/track?ai=8078&sig=0ac53a6&sid=2402&ppid=9139201&vpid=88870957&ct=offers)
D1 | MMSZ5237BT1G | Diode_SMD:D_SOD-123 | MMSZ5237BT1G | 3 | CZK 2.01 | CZK 6.04 | 11396 |  | CZK 4.69 | CZK 14.06 | MMSZ5237BT1GOSCT-ND (https://octopart.com/click/track?ai=8078&sig=00d7b6e&sid=459&ppid=332008&vpid=34061175&ct=offers) | 21375 |  | CZK 4.79 | CZK 14.36 | 1431279 (https://octopart.com/click/track?ai=8078&sig=0e67c00&sid=819&ppid=332008&vpid=139247360&ct=offers) | 41600 |  | CZK 4.69 | CZK 14.06 | 863MMSZ5237BT1G (https://octopart.com/click/track?ai=8078&sig=0cf25cc&sid=2401&ppid=332008&vpid=44862073&ct=offers) | 36000 |  | CZK 5.20 | CZK 15.60 | 58M9230 (https://octopart.com/click/track?ai=8078&sig=0033410&sid=2402&ppid=332008&vpid=190848338&ct=offers) | 20700 |  | CZK 2.01 | CZK 6.04 | 1841367 (https://octopart.com/click/track?c=1&ai=8078&sig=0ed26c2&sid=10022&ppid=332008&vpid=533255130&ct=offers)
J1 | Hirose U.FL | Connector_Coaxial:U.FL_Hirose_U.FL-R-SMT-1_Vertical | U.FL-R-SMT-1(10) | 3 | CZK 21.13 | CZK 63.39 | 91199 |  | CZK 30.69 | CZK 92.06 | H11891DKR-ND (https://octopart.com/click/track?ai=8078&sig=094afbd&sid=459&ppid=42409530&vpid=115253867&ct=offers) | 108379 |  | CZK 21.13 | CZK 63.39 | 1688077 (https://octopart.com/click/track?ai=8078&sig=07d1a95&sid=819&ppid=42409530&vpid=138889899&ct=offers) | 192027 |  | CZK 27.88 | CZK 83.63 | 798U.FLRSMT110 (https://octopart.com/click/track?ai=8078&sig=0123c20&sid=2401&ppid=42409530&vpid=115532305&ct=offers) | 13133 |  | CZK 29.98 | CZK 89.95 | 50P8856 (https://octopart.com/click/track?ai=8078&sig=0be4f71&sid=2402&ppid=42409530&vpid=115362191&ct=offers) | 8630 |  | CZK 34320.32 | CZK 102960.97 | 1757510 (https://octopart.com/click/track?ai=8078&sig=07174fd&sid=10022&ppid=42409530&vpid=501074506&ct=offers)
J2 | Conn_01x05 | Connector_PinHeader_2.54mm:PinHeader_1x05_P2.54mm_Vertical | 5-146274-5 | 3 | CZK 5.50 | CZK 16.50 | NonStk |  | CZK 5.50 | CZK 16.50 | 5-146274-5-ND (https://octopart.com/click/track?c=1&ai=8078&sig=04fad40&sid=459&ppid=40586684&vpid=198732471&ct=offers) | NonStk |  | CZK 13.66 | CZK 40.97 | 2967453 (https://octopart.com/click/track?c=1&ai=8078&sig=040b20e&sid=819&ppid=40586684&vpid=540390463&ct=offers) | 13428 |  | CZK 8.67 | CZK 26.00 | 57151462745 (https://octopart.com/click/track?ai=8078&sig=0b4ac39&sid=2401&ppid=40586684&vpid=244859517&ct=offers) | 28444 |  | CZK 13.12 | CZK 39.35 | 96Y2139 (https://octopart.com/click/track?ai=8078&sig=04648c6&sid=2402&ppid=40586684&vpid=271421458&ct=offers)
J3 | Conn_01x09 | Connector_PinHeader_2.54mm:PinHeader_1x09_P2.54mm_Vertical | 22-30-3093 | 3 | CZK 4.47 | CZK 13.40 | NonStk |  | CZK 4.60 | CZK 13.79 | 0022303093-ND (https://octopart.com/click/track?c=1&ai=8078&sig=0af57a3&sid=459&ppid=7676680&vpid=48465792&ct=offers) | NonStk |  | CZK 4.47 | CZK 13.40 | 3025670 (https://octopart.com/click/track?c=1&ai=8078&sig=09fc5c2&sid=819&ppid=7676680&vpid=534833261&ct=offers) | 5888 |  | CZK 10.31 | CZK 30.92 | 53822303093 (https://octopart.com/click/track?ai=8078&sig=006139f&sid=2401&ppid=7676680&vpid=475798688&ct=offers) | NonStk |  | CZK 5.27 | CZK 15.81 | 56H3321 (https://octopart.com/click/track?c=1&ai=8078&sig=0a5135c&sid=2402&ppid=7676680&vpid=524324937&ct=offers)
J4 | Conn_ARM_JTAG_SWD_10 | Connector_PinHeader_1.27mm:PinHeader_2x05_P1.27mm_Vertical | M50-3500542 (http://infocenter.arm.com/help/topic/com.arm.doc.ddi0314h/DDI0314H_coresight_components_trm.pdf) | 3 | CZK 25.80 | CZK 77.40 | 11242 |  | CZK 27.88 | CZK 83.63 | 952-1383-ND (https://octopart.com/click/track?ai=8078&sig=09c778e&sid=459&ppid=5385780&vpid=34033244&ct=offers) | 10164 |  | CZK 25.80 | CZK 77.40 | 1022305 (https://octopart.com/click/track?ai=8078&sig=0384310&sid=819&ppid=5385780&vpid=138886625&ct=offers) | 12883 |  | CZK 27.88 | CZK 83.63 | 855M503500542 (https://octopart.com/click/track?ai=8078&sig=0615797&sid=2401&ppid=5385780&vpid=37727554&ct=offers) | 1332 |  | CZK 28.81 | CZK 86.44 | 87K0158 (https://octopart.com/click/track?ai=8078&sig=06652ad&sid=2402&ppid=5385780&vpid=6647452&ct=offers) | 1009 |  | CZK 55.45 | CZK 166.35 | 6811184 (https://octopart.com/click/track?ai=8078&sig=0797f16&sid=10022&ppid=5385780&vpid=199027496&ct=offers)
J5 | USB_B_Micro | Connector_USB:USB_Micro-B_Molex_47346-0001 | 47346-0001 | 3 | CZK 9.07 | CZK 27.20 | 13245 |  | CZK 24.60 | CZK 73.79 | WM17141DKR-ND (https://octopart.com/click/track?ai=8078&sig=0335d17&sid=459&ppid=7164928&vpid=50127119&ct=offers) | 28000 |  | CZK 21.22 | CZK 63.65 | 1568026 (https://octopart.com/click/track?ai=8078&sig=09fb2b5&sid=819&ppid=7164928&vpid=139015539&ct=offers) | 29747 |  | CZK 22.25 | CZK 66.76 | 538473460001 (https://octopart.com/click/track?ai=8078&sig=02695e0&sid=2401&ppid=7164928&vpid=37677377&ct=offers) | 21131 |  | CZK 9.07 | CZK 27.20 | 96M8533 (https://octopart.com/click/track?ai=8078&sig=07320a8&sid=2402&ppid=7164928&vpid=11784317&ct=offers) | 310 |  | CZK 20.90 | CZK 62.69 | 7025475 (https://octopart.com/click/track?ai=8078&sig=0ecbcb7&sid=10022&ppid=7164928&vpid=199068424&ct=offers)
JP1 | Jumper | Jumper:SolderJumper-2_P1.3mm_Bridged_Pad1.0x1.5mm |  | 3 | CZK 0.00 | CZK 0.00
L1,L2 | 470n | Inductor_SMD:L_0805_2012Metric | LQM21NNR47K10D | 6 | CZK 4.14 | CZK 24.86 | 20585 |  | CZK 5.15 | CZK 30.92 | 490-1116-1-ND (https://octopart.com/click/track?ai=8078&sig=0a601e2&sid=459&ppid=387425&vpid=1442213&ct=offers) | 5189 |  | CZK 4.64 | CZK 27.84 | 9527931 (https://octopart.com/click/track?ai=8078&sig=0769e7e&sid=819&ppid=387425&vpid=139142576&ct=offers) | 18549 |  | CZK 5.15 | CZK 30.92 | 81LQG21NR47K10 (https://octopart.com/click/track?ai=8078&sig=0155ae3&sid=2401&ppid=387425&vpid=38924382&ct=offers) | 1709 |  | CZK 5.15 | CZK 30.92 | 97K3786 (https://octopart.com/click/track?ai=8078&sig=0af6667&sid=2402&ppid=387425&vpid=6686272&ct=offers) | NonStk |  | CZK 4.14 | CZK 24.86 | 7242765 (https://octopart.com/click/track?c=1&ai=8078&sig=0a3f1c7&sid=10022&ppid=387425&vpid=199073152&ct=offers)
R1,R2 | 1k | Resistor_SMD:R_0805_2012Metric | RT0805FRE101KL | 6 | CZK 2.81 | CZK 16.87 |  |  |  |  |  |  |  |  |  |  | 11150 |  | CZK 2.81 | CZK 16.87 | 603RT0805FRE101KL (https://octopart.com/click/track?ai=8078&sig=09cacf2&sid=2401&ppid=30512396&vpid=475503034&ct=offers)
R3,R4 | 2R | Resistor_SMD:R_0805_2012Metric | RT0603FRE072RL | 6 | CZK 0.25 | CZK 1.52 | NonStk |  | CZK 0.25 | CZK 1.52 | RT0603FRE072RL-ND (https://octopart.com/click/track?c=1&ai=8078&sig=0819158&sid=459&ppid=87214519&vpid=448811708&ct=offers) |  |  |  |  |  | 18050 |  | CZK 2.81 | CZK 16.87 | 603RT0603FRE072RL (https://octopart.com/click/track?ai=8078&sig=0b9bceb&sid=2401&ppid=87214519&vpid=474034384&ct=offers)
R5 | 10k | Resistor_SMD:R_0805_2012Metric | RT0805FRE0710KL | 3 | CZK 2.34 | CZK 7.03 | 91764 |  | CZK 2.34 | CZK 7.03 | YAG1239CT-ND (https://octopart.com/click/track?ai=8078&sig=051a554&sid=459&ppid=40301150&vpid=115141728&ct=offers) | 4080 |  | CZK 2.50 | CZK 7.49 | 1500664 (https://octopart.com/click/track?ai=8078&sig=036b469&sid=819&ppid=40301150&vpid=478819612&ct=offers) | 182565 |  | CZK 2.81 | CZK 8.43 | 603RT0805FRE0710KL (https://octopart.com/click/track?ai=8078&sig=0f0c3b2&sid=2401&ppid=40301150&vpid=114830382&ct=offers) | 5254 |  | CZK 2.81 | CZK 8.43 | 62M2341 (https://octopart.com/click/track?ai=8078&sig=026f511&sid=2402&ppid=40301150&vpid=115424753&ct=offers)
R6 | 2k | Resistor_SMD:R_0805_2012Metric | RT0805FRE072KL | 3 | CZK 2.34 | CZK 7.03 | 20591 |  | CZK 2.34 | CZK 7.03 | YAG3362CT-ND (https://octopart.com/click/track?ai=8078&sig=048127e&sid=459&ppid=1191348&vpid=225547370&ct=offers) |  |  |  |  |  | 31875 |  | CZK 2.81 | CZK 8.43 | 603RT0805FRE072KL (https://octopart.com/click/track?ai=8078&sig=0e2c298&sid=2401&ppid=1191348&vpid=99295377&ct=offers)
R7,R8,R10,R11 | 4k7 | Resistor_SMD:R_0805_2012Metric | RT0805FRE134K7L | 12 | CZK 1.50 | CZK 17.99 |  |  |  |  |  |  |  |  |  |  | 2377 |  | CZK 1.50 | CZK 17.99 | 603RT0805FRE134K7L (https://octopart.com/click/track?ai=8078&sig=05aea21&sid=2401&ppid=16262042&vpid=475503089&ct=offers)
R9 | 10m | Resistor_SMD:R_0805_2012Metric | CFN0805-FX-R010ELF | 3 | CZK 2.04 | CZK 6.11 | 3229 |  | CZK 14.52 | CZK 43.57 | CFN0805-FX-R010ELFCT-ND (https://octopart.com/click/track?ai=8078&sig=039551e&sid=459&ppid=99170685&vpid=539846255&ct=offers) |  |  |  |  |  | 9595 |  | CZK 12.42 | CZK 37.25 | 652CFN0805FXR010ELF (https://octopart.com/click/track?ai=8078&sig=0b8e4af&sid=2401&ppid=99170685&vpid=530665756&ct=offers) | NonStk |  | CZK 2.04 | CZK 6.11 | 34AH0417 (https://octopart.com/click/track?c=1&ai=8078&sig=0430152&sid=2402&ppid=99170685&vpid=587880433&ct=offers)
SW1,SW2 | SW_Push | Connector_PinHeader_1.27mm:PinHeader_1x02_P1.27mm_Vertical | M50-3530242 | 6 | CZK 1.52 | CZK 9.11 | 13952 |  | CZK 2.81 | CZK 16.87 | 952-3598-ND (https://octopart.com/click/track?ai=8078&sig=0a6a160&sid=459&ppid=81691170&vpid=420430275&ct=offers) | 5410 |  | CZK 1.52 | CZK 9.11 | 3226045 (https://octopart.com/click/track?ai=8078&sig=0872342&sid=819&ppid=81691170&vpid=579539847&ct=offers) | 129 |  | CZK 2.58 | CZK 15.46 | 855M503530242 (https://octopart.com/click/track?ai=8078&sig=0a5d087&sid=2401&ppid=81691170&vpid=420425386&ct=offers) | NonStk |  | CZK 2.11 | CZK 12.65 | 52AC5102 (https://octopart.com/click/track?c=1&ai=8078&sig=0be3318&sid=2402&ppid=81691170&vpid=537779981&ct=offers)
TP1 | SDI1_TP | TestPoint:TestPoint_Loop_D2.50mm_Drill1.0mm_LowProfile |  | 3 | CZK 0.00 | CZK 0.00
TP2 | SDO1_TP | TestPoint:TestPoint_Loop_D2.50mm_Drill1.0mm_LowProfile |  | 3 | CZK 0.00 | CZK 0.00
TP3 | SCLK1_TP | TestPoint:TestPoint_Loop_D2.50mm_Drill1.0mm_LowProfile |  | 3 | CZK 0.00 | CZK 0.00
TP4 | CS1_TP | TestPoint:TestPoint_Loop_D2.50mm_Drill1.0mm_LowProfile |  | 3 | CZK 0.00 | CZK 0.00
TP5 | AK1_TP | TestPoint:TestPoint_Loop_D2.50mm_Drill1.0mm_LowProfile |  | 3 | CZK 0.00 | CZK 0.00
TP6,TP9 | I2C_D2_TP | TestPoint:TestPoint_Loop_D2.50mm_Drill1.0mm_LowProfile |  | 6 | CZK 0.00 | CZK 0.00
TP7 | I2C_C2_TP | TestPoint:TestPoint_Loop_D2.50mm_Drill1.0mm_LowProfile |  | 3 | CZK 0.00 | CZK 0.00
TP8 | I2C_C1_TP | TestPoint:TestPoint_Loop_D2.50mm_Drill1.0mm_LowProfile |  | 3 | CZK 0.00 | CZK 0.00
U1 | INNOCOMM-SN10-11 | Antenna:InnoCommSN10-11 | SN10-11-INNO | 3 | CZK 0.00 | CZK 0.00
U2 | MPC17531ATEJ | Package_SO:HTSSOP-20-1EP_4.4x6.5mm_P0.65mm_EP3.4x6.5mm_ThermalVias | MPC17531ATEJ (https://www.nxp.com/docs/en/data-sheet/MPC17531A.pdf) | 3 | CZK 52.71 | CZK 158.12 | 18 |  | CZK 58.56 | CZK 175.69 | 568-13357-ND (https://octopart.com/click/track?ai=8078&sig=09317b4&sid=459&ppid=73850212&vpid=416508912&ct=offers) | 38 |  | CZK 60.70 | CZK 182.11 | 2890075 (https://octopart.com/click/track?ai=8078&sig=005b9e6&sid=819&ppid=73850212&vpid=492583869&ct=offers) | 1986 |  | CZK 58.56 | CZK 175.69 | 841MPC17531ATEJ (https://octopart.com/click/track?ai=8078&sig=0f50364&sid=2401&ppid=73850212&vpid=273368650&ct=offers) | 38 |  | CZK 52.71 | CZK 158.12 | 61AC0707 (https://octopart.com/click/track?ai=8078&sig=02ee399&sid=2402&ppid=73850212&vpid=492708563&ct=offers)
U3 | K32L2B21VLH0A | Package_QFP:LQFP-64_10x10mm_P0.5mm | K32L2B21VLH0A | 3 | CZK 69.43 | CZK 208.30 | NonStk |  | CZK 69.43 | CZK 208.30 | 568-K32L2B21VLH0A-ND (https://octopart.com/click/track?c=1&ai=8078&sig=05c887b&sid=459&ppid=104793564&vpid=594403904&ct=offers) |  |  |  |  |  | NonStk |  | CZK 94.17 | CZK 282.51 | 771K32L2B21VLH0A (https://octopart.com/click/track?c=1&ai=8078&sig=0fded7e&sid=2401&ppid=104793564&vpid=594218781&ct=offers) | NonStk |  | CZK 92.76 | CZK 278.29 | 33AH2740 (https://octopart.com/click/track?c=1&ai=8078&sig=01e85bd&sid=2402&ppid=104793564&vpid=585370818&ct=offers)
U4 | MCP73831-2-OT | Package_TO_SOT_SMD:SOT-23-5 | MCP73831T-3ACI/OT (http://ww1.microchip.com/downloads/en/DeviceDoc/20001984g.pdf) | 3 | CZK 10.45 | CZK 31.34 | 1886 |  | CZK 13.12 | CZK 39.35 | MCP73831T-3ACI/OTDKR-ND (https://octopart.com/click/track?ai=8078&sig=0d5eff0&sid=459&ppid=422784&vpid=188043934&ct=offers) | 2770 |  | CZK 13.57 | CZK 40.71 | 2920755 (https://octopart.com/click/track?ai=8078&sig=00c077e&sid=819&ppid=422784&vpid=508132267&ct=offers) | 5911 |  | CZK 13.12 | CZK 39.35 | 579MCP73831T3ACIOT (https://octopart.com/click/track?ai=8078&sig=0ac65a7&sid=2401&ppid=422784&vpid=113437821&ct=offers) | 2755 |  | CZK 10.45 | CZK 31.34 | 72AC6172 (https://octopart.com/click/track?ai=8078&sig=0d7f8b2&sid=2402&ppid=422784&vpid=508653776&ct=offers)
U5 | LTC2941CMS8E | Package_SO:MSOP-8-1EP_3x3mm_P0.65mm_EP1.68x1.88mm | LTC2941CMS8E#PBF (http://cds.linear.com/docs/en/datasheet/2941fb.pdf) | 3 | CZK 73.25 | CZK 219.76 | 222 |  | CZK 76.37 | CZK 229.10 | LTC2941CMS8E#PBF-ND (https://octopart.com/click/track?ai=8078&sig=0e8ccb6&sid=459&ppid=88944225&vpid=255201878&ct=offers) | NonStk |  | CZK 73.25 | CZK 219.76 | 2531543 (https://octopart.com/click/track?c=1&ai=8078&sig=0a407c4&sid=819&ppid=88944225&vpid=254502844&ct=offers) | 337 |  | CZK 76.37 | CZK 229.10 | 584LTC2941CMS8E#PBF (https://octopart.com/click/track?ai=8078&sig=069bed7&sid=2401&ppid=88944225&vpid=460729054&ct=offers)
U6 | TPS78330 | Package_TO_SOT_SMD:SOT-23-5 | C0805C475K8PACTU (http://www.ti.com/lit/ds/symlink/tps783.pdf) | 3 | CZK 1.93 | CZK 5.78 | 243099 |  | CZK 6.09 | CZK 18.27 | 399-3133-1-ND (https://octopart.com/click/track?ai=8078&sig=006f170&sid=459&ppid=107582&vpid=1698235&ct=offers) | 217500 |  | CZK 2.95 | CZK 8.84 | 2409055 (https://octopart.com/click/track?ai=8078&sig=09b40ce&sid=819&ppid=107582&vpid=138967804&ct=offers) | 70384 |  | CZK 3.98 | CZK 11.95 | 80C0805C475K8P (https://octopart.com/click/track?ai=8078&sig=0d66b76&sid=2401&ppid=107582&vpid=44737003&ct=offers) | 35000 |  | CZK 8.71 | CZK 26.14 | 70K9144 (https://octopart.com/click/track?ai=8078&sig=08b9cc6&sid=2402&ppid=107582&vpid=16452459&ct=offers) | 32150 |  | CZK 1.93 | CZK 5.78 | 4516284 (https://octopart.com/click/track?ai=8078&sig=09077a8&sid=10022&ppid=107582&vpid=199040127&ct=offers)
U7 | PN7150 | Package_DFN_QFN:QFN-40-1EP_6x6mm_P0.5mm_EP4.6x4.6mm_ThermalVias | PN7150B0HN/C11004Y (https://www.nxp.com/docs/en/data-sheet/PN7120.pdf) | 3 | CZK 85.81 | CZK 257.44 | NonStk |  | CZK 85.81 | CZK 257.44 | 568-PN7150B0HN/C11004YTR-ND (https://octopart.com/click/track?c=1&ai=8078&sig=003e247&sid=459&ppid=104793589&vpid=594668667&ct=offers) |  |  |  |  |  | 11898 |  | CZK 156.95 | CZK 470.85 | 771PN7150B0HNC1104Y (https://octopart.com/click/track?ai=8078&sig=069f1a4&sid=2401&ppid=104793589&vpid=586609837&ct=offers) | NonStk |  | CZK 92.53 | CZK 277.59 | 33AH2843 (https://octopart.com/click/track?c=1&ai=8078&sig=07b7eb0&sid=2402&ppid=104793589&vpid=585370926&ct=offers)
Y1 | 27.12 MHz XRCGB27M120F3M10R0 | Crystal:Crystal_SMD_2016-4Pin_2.0x1.6mm |  | 3 | CZK 0.00 | CZK 0.00
 | Used currency rates: |  |  |  | Total Purchase: | CZK 0.00 |  |  |  | CZK 0.00 |  |  |  |  | CZK 0.00 |  |  |  |  | CZK 0.00 |  |  |  |  | CZK 0.00 |  |  |  |  | CZK 0.00
 | CZK(CZK)/USD($): | 23.42531439 |  |  | Purchase description:
 | CZK(CZK)/GBP(£): | 29.1839495
KiCost® v.1.1.2

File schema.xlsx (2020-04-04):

Prj: | Smartlock |  |  |  | Board Qty: | 100
Co.: | Marek Vitula |  |  |  | Unit Cost: | 0.00
Prj date: | 12/9/2019 9:29:18 PM |  |  |  | Total Cost: | 0.00 |  |  |  | 0.00 | 0 |  |  |  | 0.00 | 0 |  |  |  | 0.00 | 0 |  |  |  | 0.00 | 0 |  |  |  | 0.00 | 0
$ date: | 2019-12-09 21:32:31
Global Part Info |  |  |  |  |  |  | Digi-Key |  |  |  |  | Farnell |  |  |  |  | Mouser |  |  |  |  | Newark |  |  |  |  | Rs Components
Refs | Value | Footprint | Manf# | Qty | Unit$ | Ext$ | Avail | Purch | Unit$ | Ext$ | Cat# | Avail | Purch | Unit$ | Ext$ | Cat# | Avail | Purch | Unit$ | Ext$ | Cat# | Avail | Purch | Unit$ | Ext$ | Cat# | Avail | Purch | Unit$ | Ext$ | Cat#
AE1 | Antenna | Antenna:nfc_40_75 |  | 0 | 0.00 | 0.00
BT1 | Battery_Cell | Battery:BatteryHolder_MPD_BH-18650-PC2 | BK-18650-PC2 | 0 | 0.00 | 0.00 | 2094 |  | 0.00 | 0.00 | BK-18650-PC2-ND (https://octopart.com/click/track?c=1&ai=8078&sig=0df057f&sid=459&ppid=10598814&vpid=33662670&ct=offers)
C1 | 33p | Capacitor_SMD:C_0805_2012Metric | C0805C330K5HACAUTO | 0 | 0.00 | 0.00 | NonStk |  | 0.00 | 0.00 | C0805C330K5HACAUTO-ND (https://octopart.com/click/track?c=1&ai=8078&sig=0fb1fde&sid=459&ppid=88095168&vpid=456007969&ct=offers) |  |  |  |  |  | 11408 |  | 0.00 | 0.00 | 80C0805C330K5HAUTO (https://octopart.com/click/track?ai=8078&sig=0177dc9&sid=2401&ppid=88095168&vpid=458161513&ct=offers)
C11,C12 | 250p/16V | Capacitor_SMD:C_0805_2012Metric | 08055A251JAT2A | 0 | 0.00 | 0.00 | NonStk |  |  |  | 08055A251JAT2A-ND (https://octopart.com/click/track?c=1&ai=8078&sig=090d1b3&sid=459&ppid=8665191&vpid=33541788&ct=offers) |  |  |  |  |  | 18712 |  | 0.00 | 0.00 | 58108055A251JAT2A (https://octopart.com/click/track?ai=8078&sig=033ec15&sid=2401&ppid=8665191&vpid=457557647&ct=offers)
C13,C14 | 30p/50V | Capacitor_SMD:C_0805_2012Metric | 08055A300GAT2A | 0 | 0.00 | 0.00 | NonStk |  | 0.00 | 0.00 | 08055A300GAT2A-ND (https://octopart.com/click/track?c=1&ai=8078&sig=0358c8e&sid=459&ppid=9080631&vpid=33541825&ct=offers) |  |  |  |  |  | 275 |  | 0.00 | 0.00 | 58108055A300GAT2A (https://octopart.com/click/track?ai=8078&sig=071dcd3&sid=2401&ppid=9080631&vpid=456348598&ct=offers)
C15,C16 | 150p/50V | Capacitor_SMD:C_0805_2012Metric | 08055A151FAT2A | 0 | 0.00 | 0.00 | 61070 |  | 0.00 | 0.00 | 478-6219-6-ND (https://octopart.com/click/track?ai=8078&sig=09822c0&sid=459&ppid=2337672&vpid=34028323&ct=offers) | 16000 |  | 0.00 | 0.00 | 2918696 (https://octopart.com/click/track?ai=8078&sig=059797a&sid=819&ppid=2337672&vpid=500011276&ct=offers) | 25794 |  | 0.00 | 0.00 | 58108055A151FAT2A (https://octopart.com/click/track?ai=8078&sig=0ee936d&sid=2401&ppid=2337672&vpid=44735610&ct=offers) | 16000 |  | 0.00 | 0.00 | 96Y8488 (https://octopart.com/click/track?ai=8078&sig=0d7a7d0&sid=2402&ppid=2337672&vpid=271948959&ct=offers) | 19600 |  | 0.00 | 0.00 | 1359034 (https://octopart.com/click/track?c=1&ai=8078&sig=01a8ddf&sid=10022&ppid=2337672&vpid=500984126&ct=offers)
C2 | 47u/10V | Capacitor_Tantalum_SMD:CP_EIA-3528-21_Kemet-B | TPSB476M010T0250 | 0 | 0.00 | 0.00 | NonStk |  | 0.00 | 0.00 | 478-TPSB476M010T0250TR-ND (https://octopart.com/click/track?c=1&ai=8078&sig=09a8646&sid=459&ppid=47029682&vpid=596809048&ct=offers) |  |  |  |  |  | 1782 |  | 0.00 | 0.00 | 581TPSB476M010T0250 (https://octopart.com/click/track?ai=8078&sig=00f6d83&sid=2401&ppid=47029682&vpid=330475144&ct=offers)
C28,C32-C34,C37 | 1u | Capacitor_SMD:C_0805_2012Metric | C0805C105K8RACTU | 0 | 0.00 | 0.00 | 251117 |  | 0.00 | 0.00 | 399-1172-6-ND (https://octopart.com/click/track?ai=8078&sig=0a9ccea&sid=459&ppid=103379&vpid=34044386&ct=offers) | 36000 |  | 0.00 | 0.00 | 2409048 (https://octopart.com/click/track?ai=8078&sig=0d0e397&sid=11744&ppid=103379&vpid=133110117&ct=offers) | 173571 |  | 0.00 | 0.00 | 80C0805C105K8R (https://octopart.com/click/track?ai=8078&sig=09c9d55&sid=2401&ppid=103379&vpid=44736975&ct=offers) | 20000 |  | 0.00 | 0.00 | 64K2894 (https://octopart.com/click/track?ai=8078&sig=05fac39&sid=2402&ppid=103379&vpid=16452352&ct=offers) | 27000 |  | 0.00 | 0.00 | 8692149 (https://octopart.com/click/track?c=1&ai=8078&sig=03b1c91&sid=10022&ppid=103379&vpid=562613324&ct=offers)
C3,C4,C25-C27,C36 | 4.7u | Capacitor_SMD:C_0805_2012Metric | C0805C475K8PACTU | 0 | 0.00 | 0.00 | 243099 |  | 0.00 | 0.00 | 399-3133-1-ND (https://octopart.com/click/track?ai=8078&sig=006f170&sid=459&ppid=107582&vpid=1698235&ct=offers) | 217500 |  | 0.00 | 0.00 | 2409055 (https://octopart.com/click/track?ai=8078&sig=09b40ce&sid=819&ppid=107582&vpid=138967804&ct=offers) | 70384 |  | 0.00 | 0.00 | 80C0805C475K8P (https://octopart.com/click/track?ai=8078&sig=0d66b76&sid=2401&ppid=107582&vpid=44737003&ct=offers) | 35000 |  | 0.00 | 0.00 | 70K9144 (https://octopart.com/click/track?ai=8078&sig=08b9cc6&sid=2402&ppid=107582&vpid=16452459&ct=offers) | 32150 |  | 0.00 | 0.00 | 4516284 (https://octopart.com/click/track?ai=8078&sig=09077a8&sid=10022&ppid=107582&vpid=199040127&ct=offers)
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

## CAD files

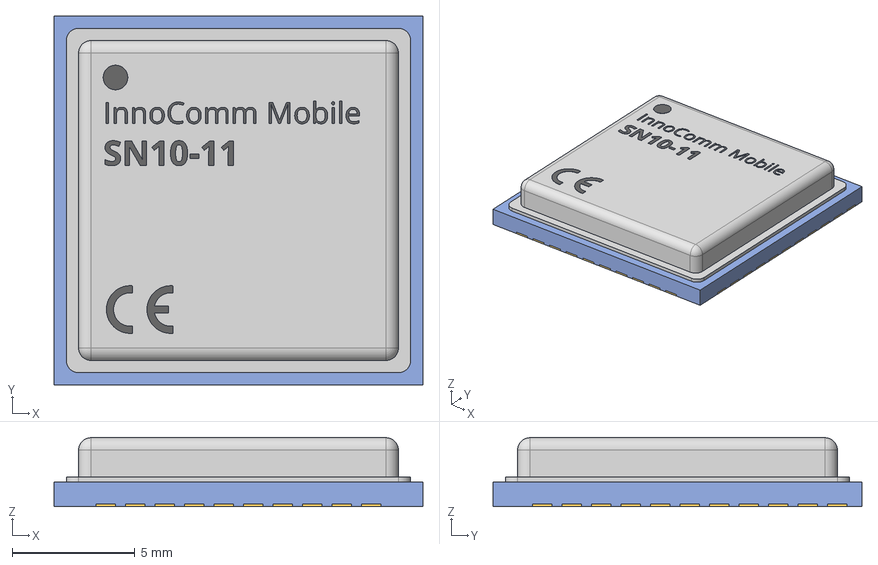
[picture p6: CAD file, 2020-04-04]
SN10-11.step
15.0 x 15.0 x 2.81 mm

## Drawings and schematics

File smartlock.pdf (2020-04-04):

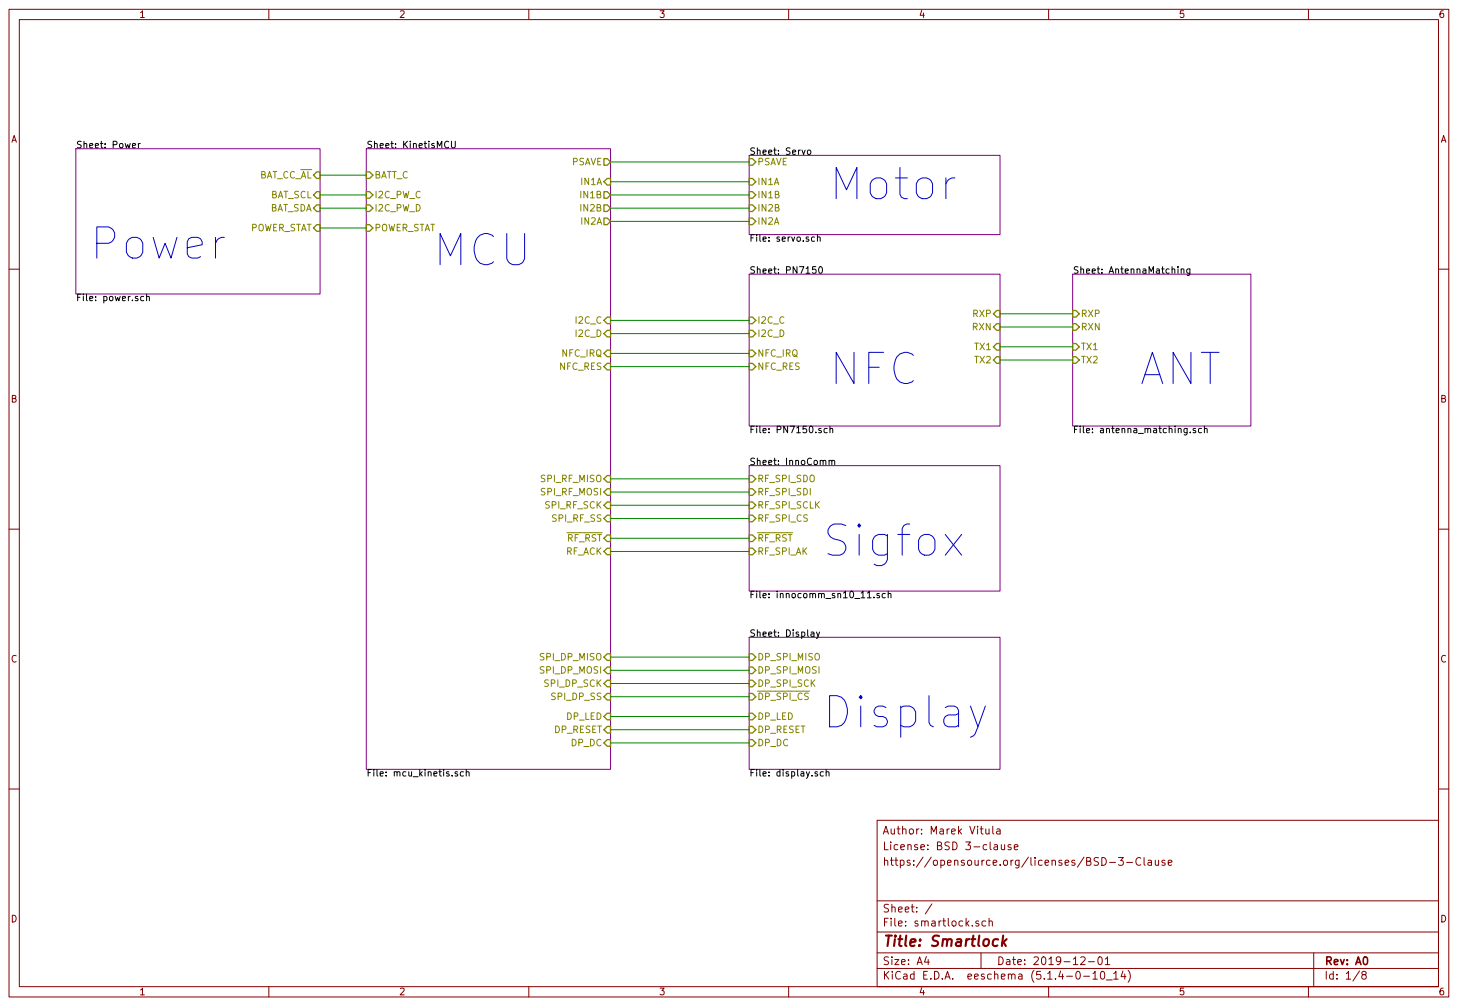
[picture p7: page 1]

File: antenna_matching.sch RXP RXN

License: BSD 3-clause Author: Marek Vitula Sheet: InnoComm
File: innocomm_sn10_11.sch RF_SPI_SDI RF_SPI_CS RF_SPI_SDO
Sigfox

File: smartlock.sch Sheet: / https://opensource.org/licenses/BSD-3-Clause

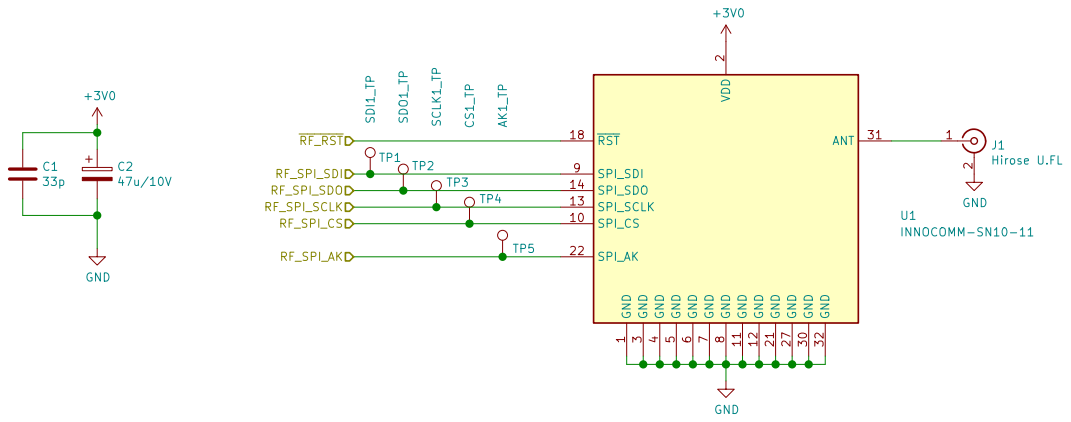
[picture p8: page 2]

1 SPI_CS 10 GND 11 GND 12 SPI_SCLK 13 SPI_SDO 14 RST 18 VDD

3 GND 30 ANT 31 GND 32 GND

License: BSD 3-clause Author: Marek Vitula GND

File: innocomm_sn10_11.sch Sheet: /InnoComm/ https://opensource.org/licenses/BSD-3-Clause

Id: 2/8 Title: Sigfox module

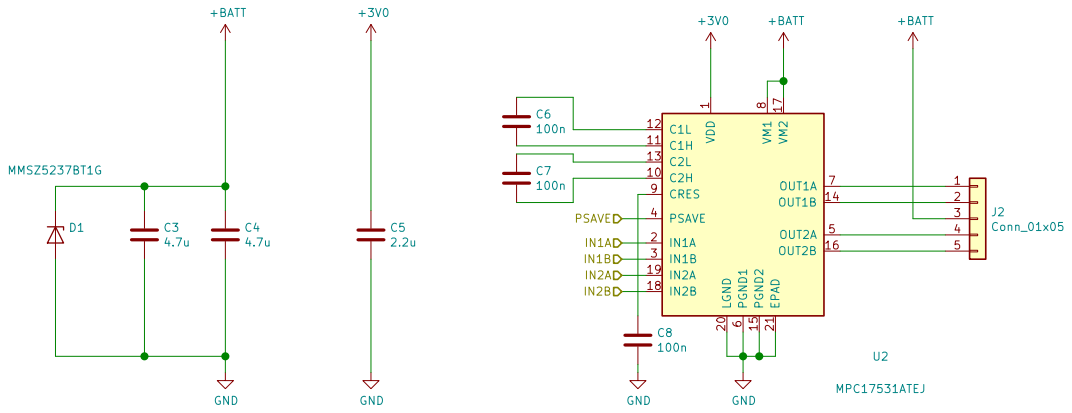
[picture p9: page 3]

License: BSD 3-clause Author: Marek Vitula C3

Id: 3/8 Title: Motor control File: servo.sch Sheet: /Servo/ https://opensource.org/licenses/BSD-3-Clause

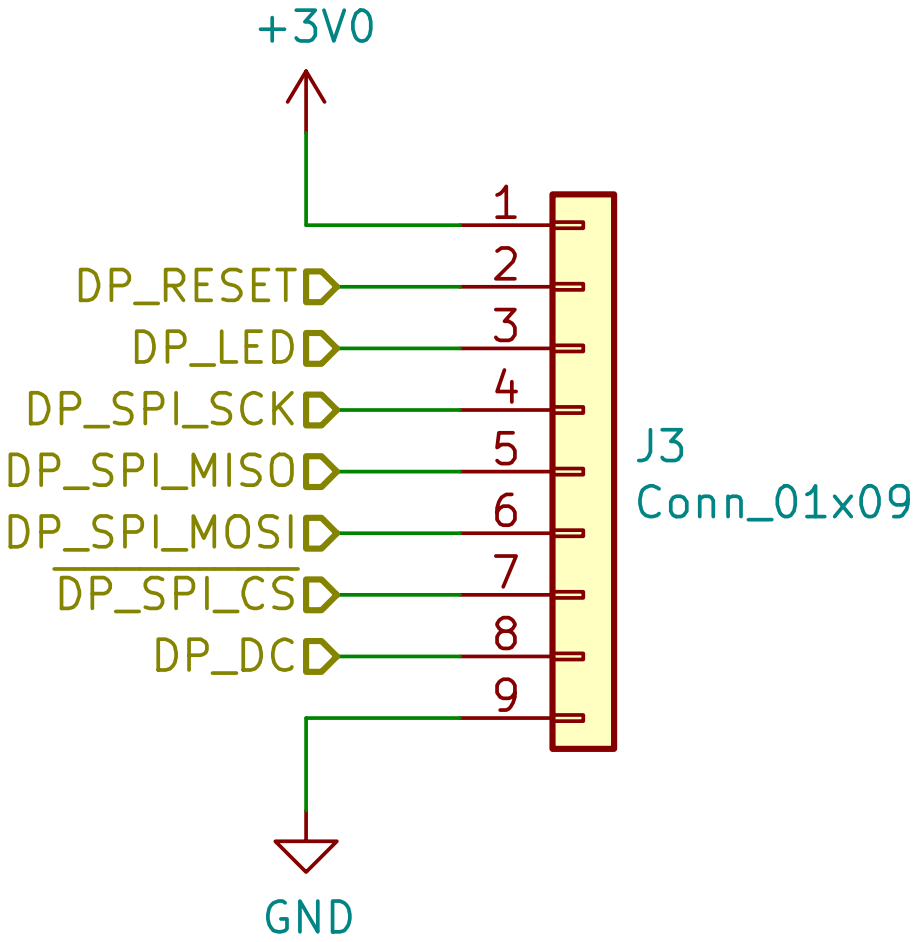
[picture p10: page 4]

License: BSD 3-clause Author: Marek Vitula

https://opensource.org/licenses/BSD-3-Clause

Sheet: /Display/
File: display.sch
Id: 4/8 Title: Display header

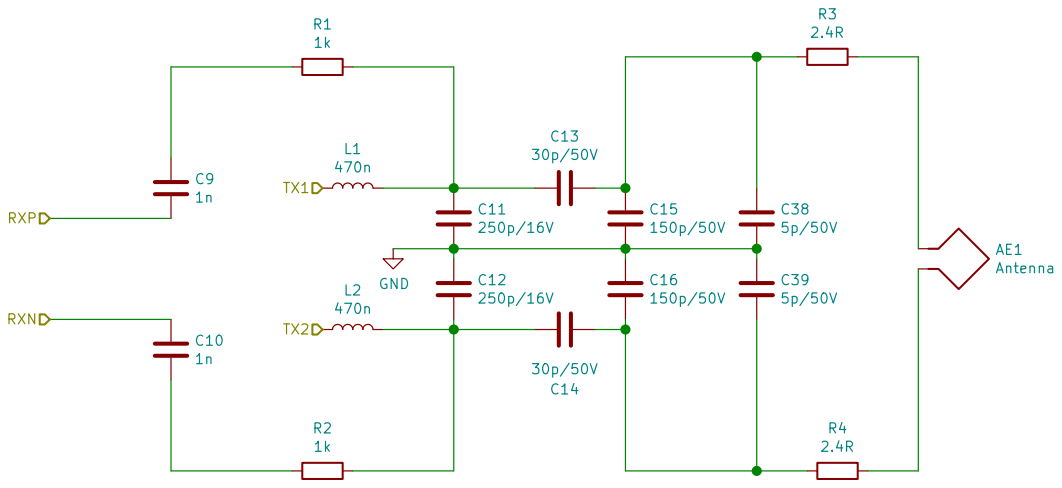
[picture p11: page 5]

License: BSD 3-clause Author: Marek Vitula C10

https://opensource.org/licenses/BSD-3-Clause

Sheet: /AntennaMatching/
File: antenna_matching.sch
Id: 5/8 Title: Antenna matching

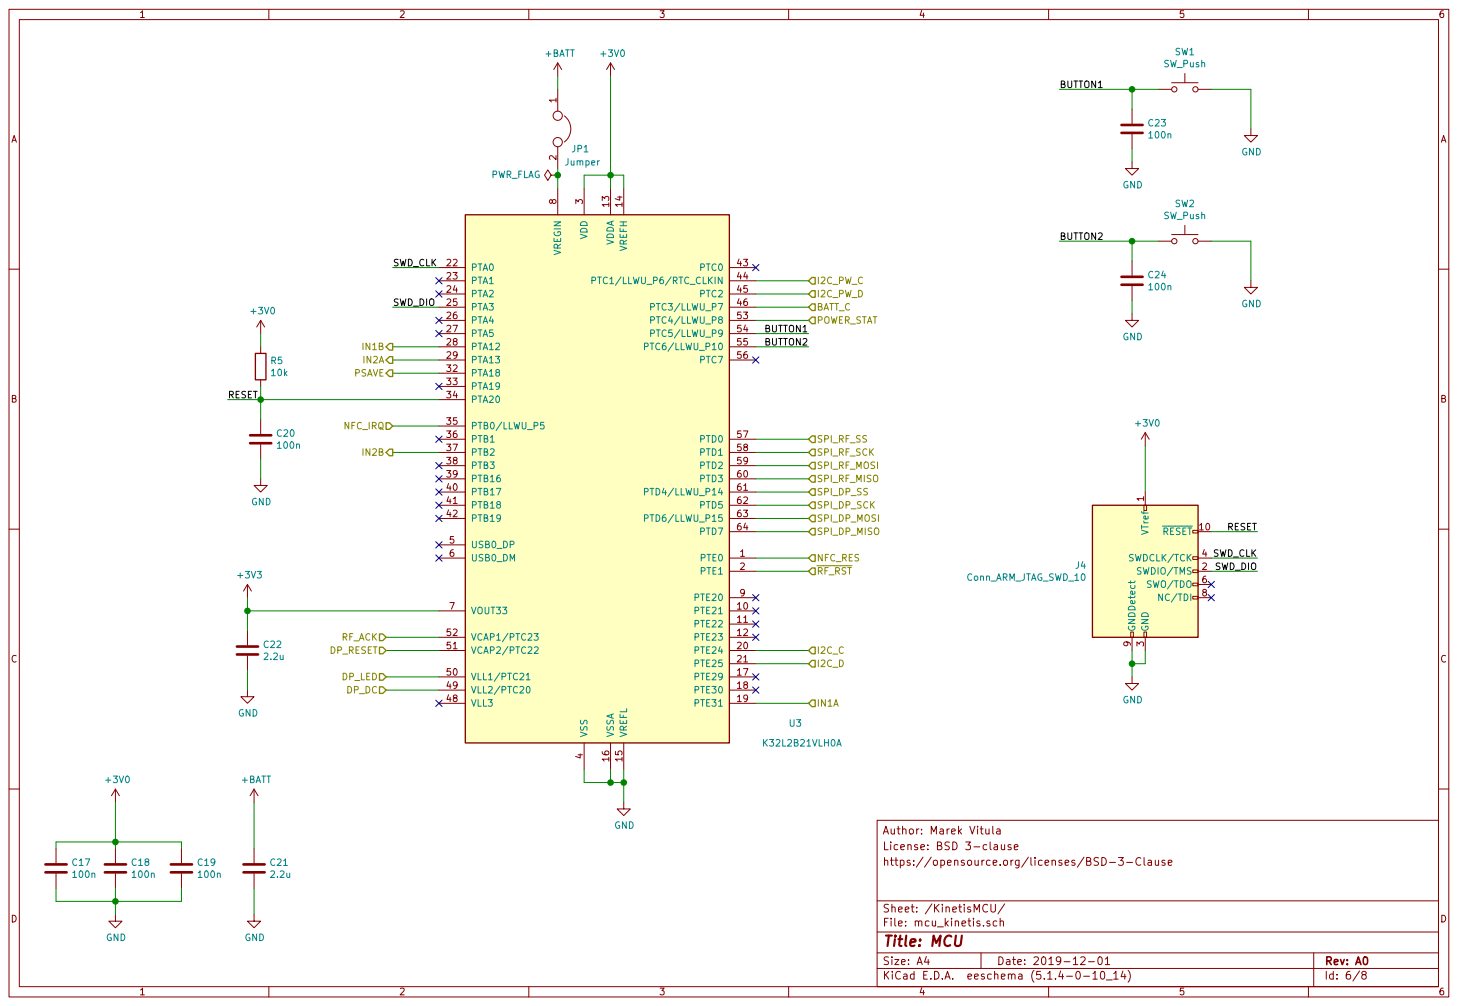
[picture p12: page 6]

8 PTE20 9 U3 K32L2B21VLH0A GND VTref 1 RESET 10 SWDIO/TMS 2 GND

3 SWDCLK/TCK 4 SWO/TDO 6 NC/TDI 8 GNDDetect 9

License: BSD 3-clause Author: Marek Vitula GND

File: mcu_kinetis.sch Sheet: /KinetisMCU/ https://opensource.org/licenses/BSD-3-Clause

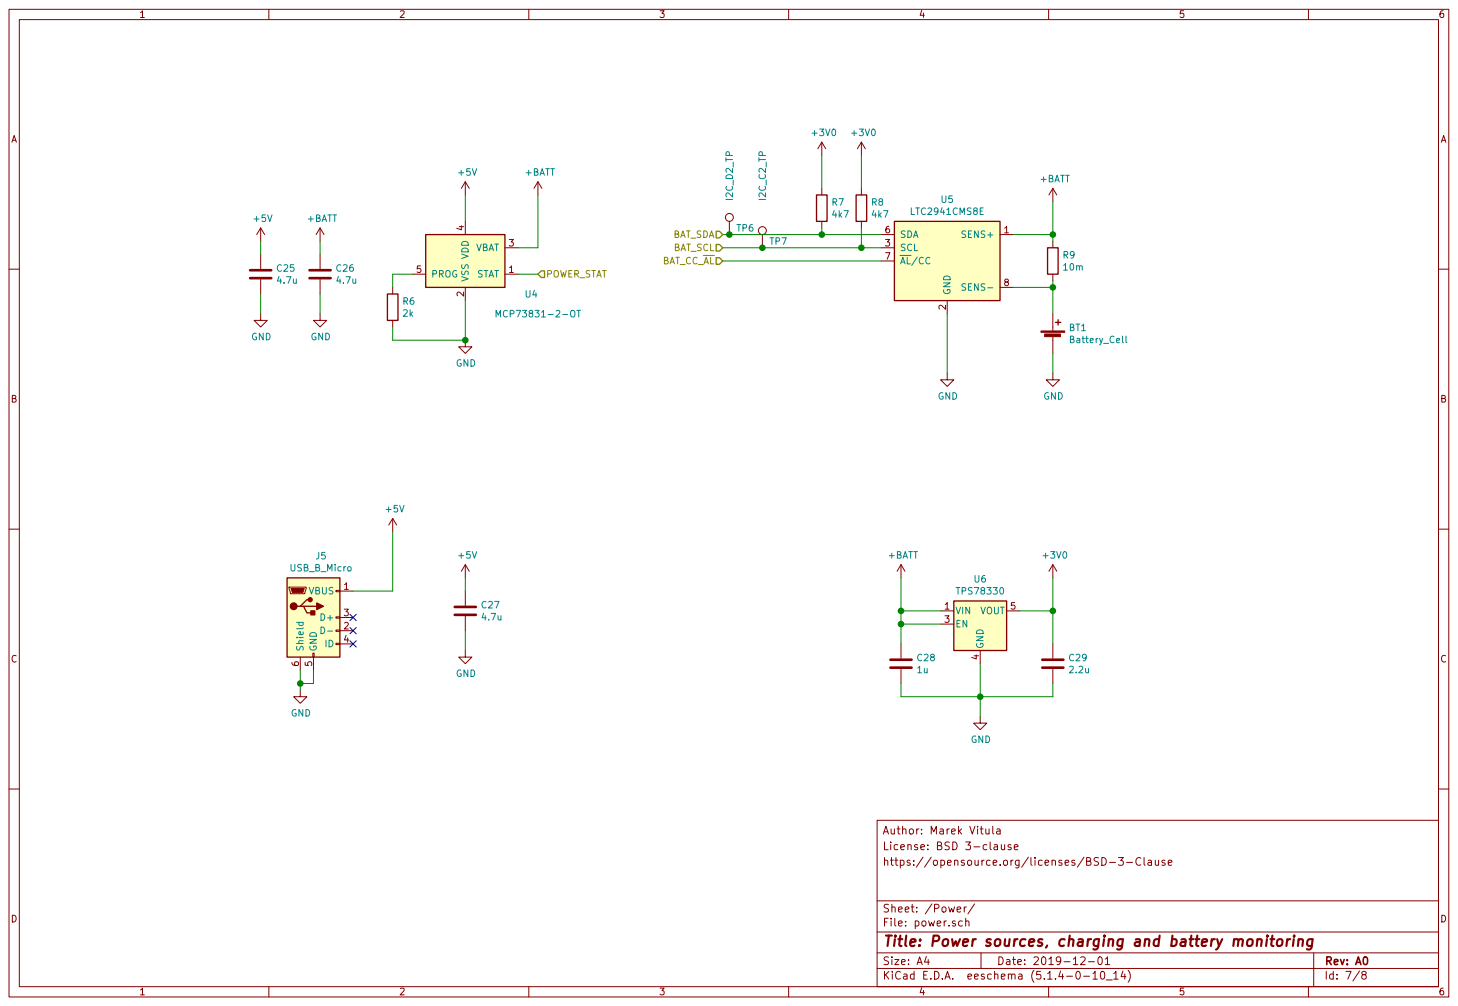
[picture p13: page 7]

4 PROG 5 U4 MCP73831-2-OT BT1 Battery_Cell +BATT GND

2 SCL 3 SDA 6 AL/CC 7 SENS- 8 U5

License: BSD 3-clause Author: Marek Vitula

File: power.sch Sheet: /Power/ https://opensource.org/licenses/BSD-3-Clause

Id: 7/8 Title: Power sources, charging and battery monitoring

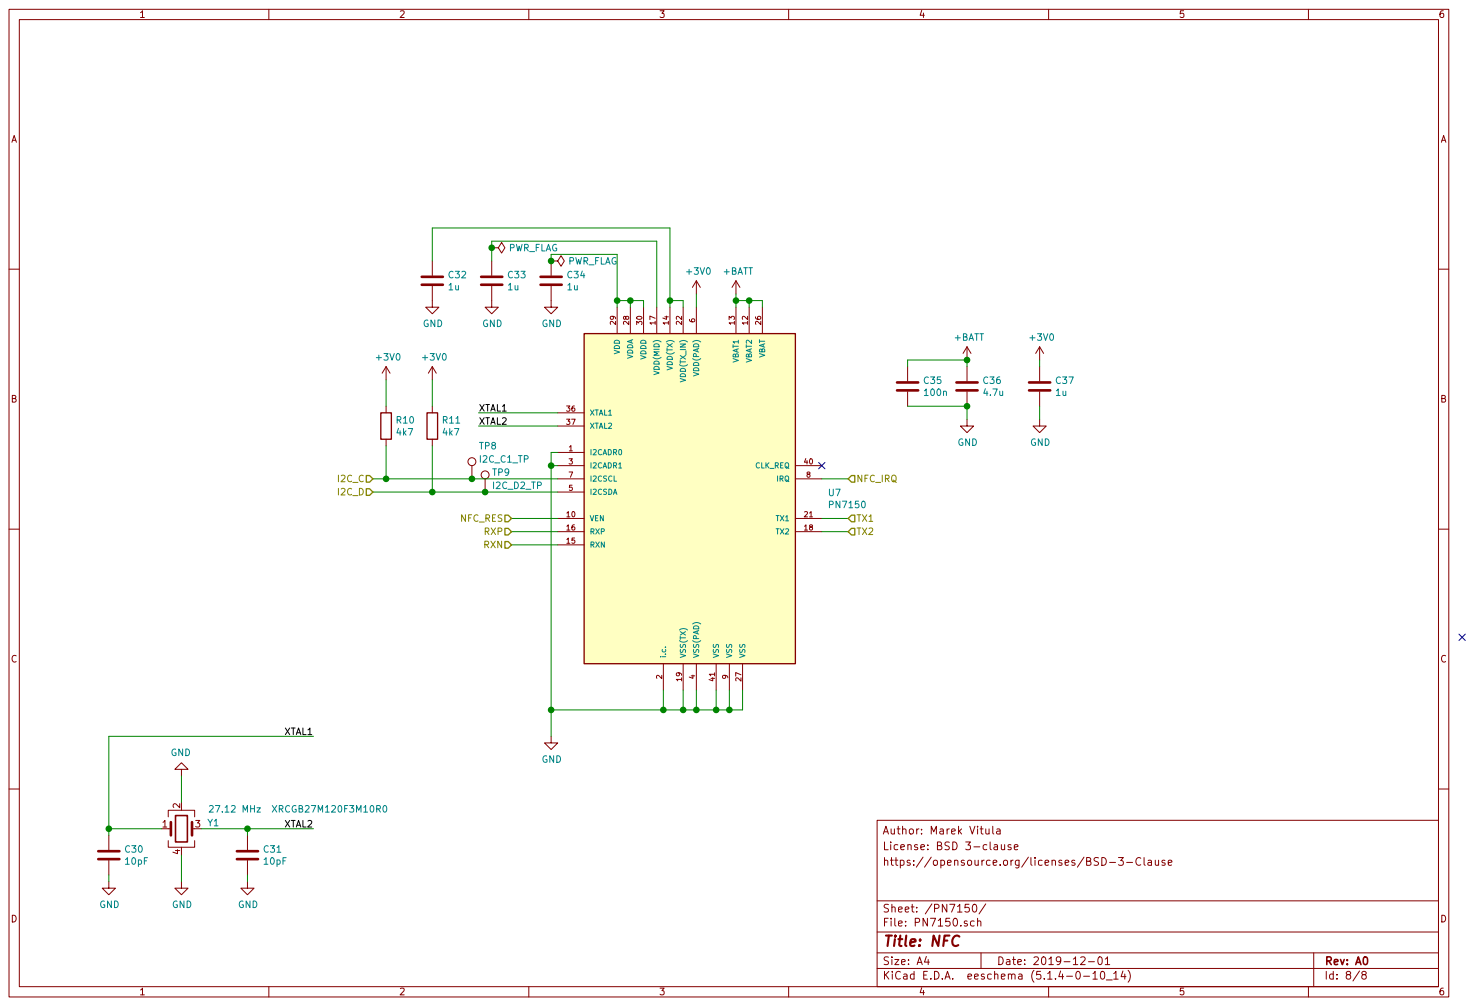
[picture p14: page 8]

9 VDD(TX_IN) 22 VSS 27 VDDA 28 VDDD 30 VSS 41

License: BSD 3-clause Author: Marek Vitula

File: PN7150.sch Sheet: /PN7150/ https://opensource.org/licenses/BSD-3-Clause

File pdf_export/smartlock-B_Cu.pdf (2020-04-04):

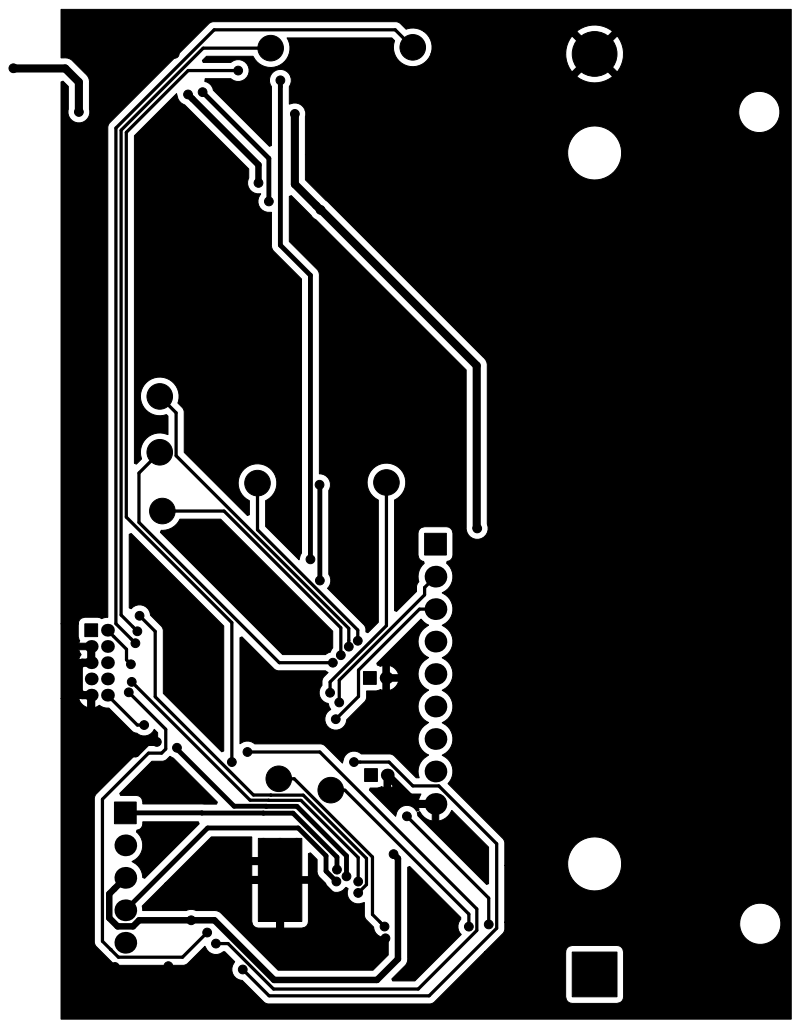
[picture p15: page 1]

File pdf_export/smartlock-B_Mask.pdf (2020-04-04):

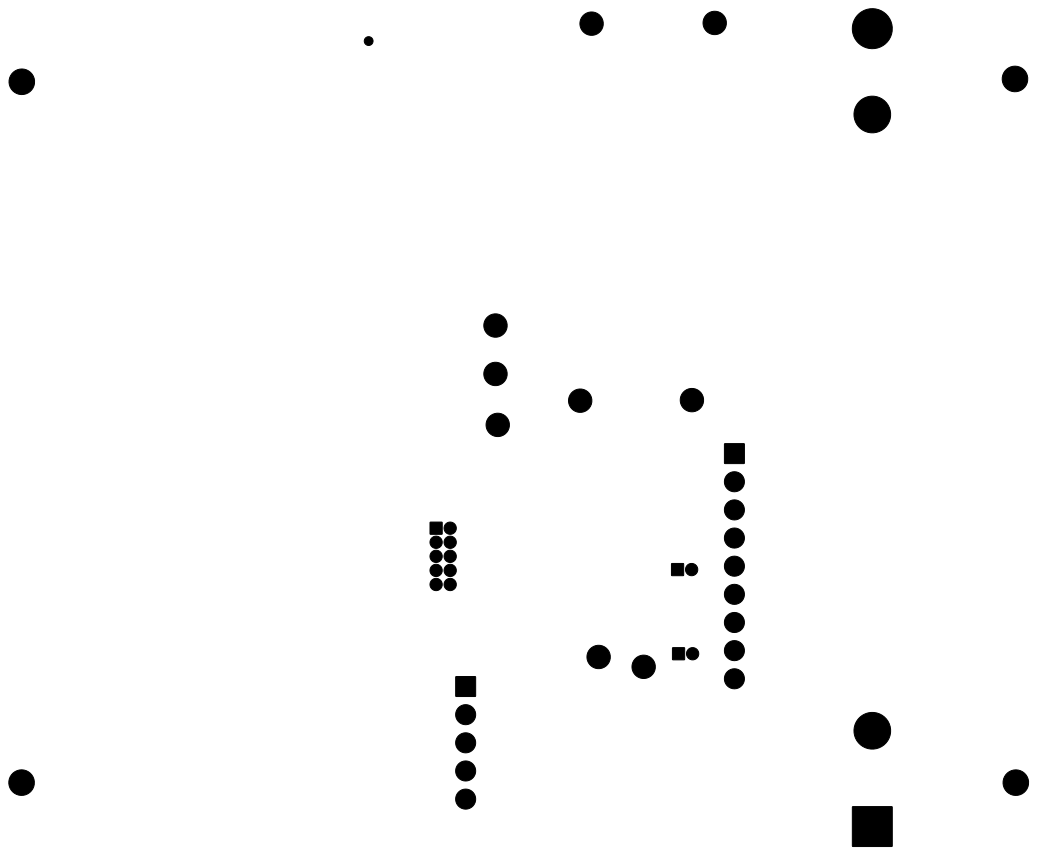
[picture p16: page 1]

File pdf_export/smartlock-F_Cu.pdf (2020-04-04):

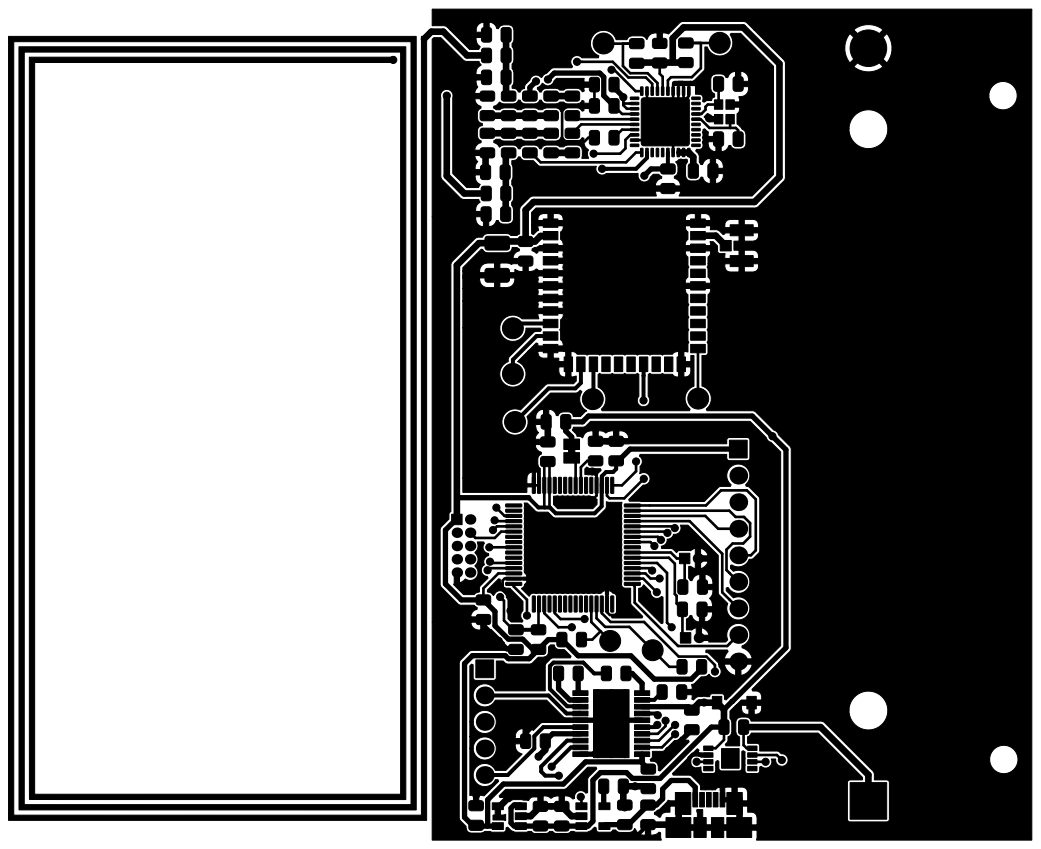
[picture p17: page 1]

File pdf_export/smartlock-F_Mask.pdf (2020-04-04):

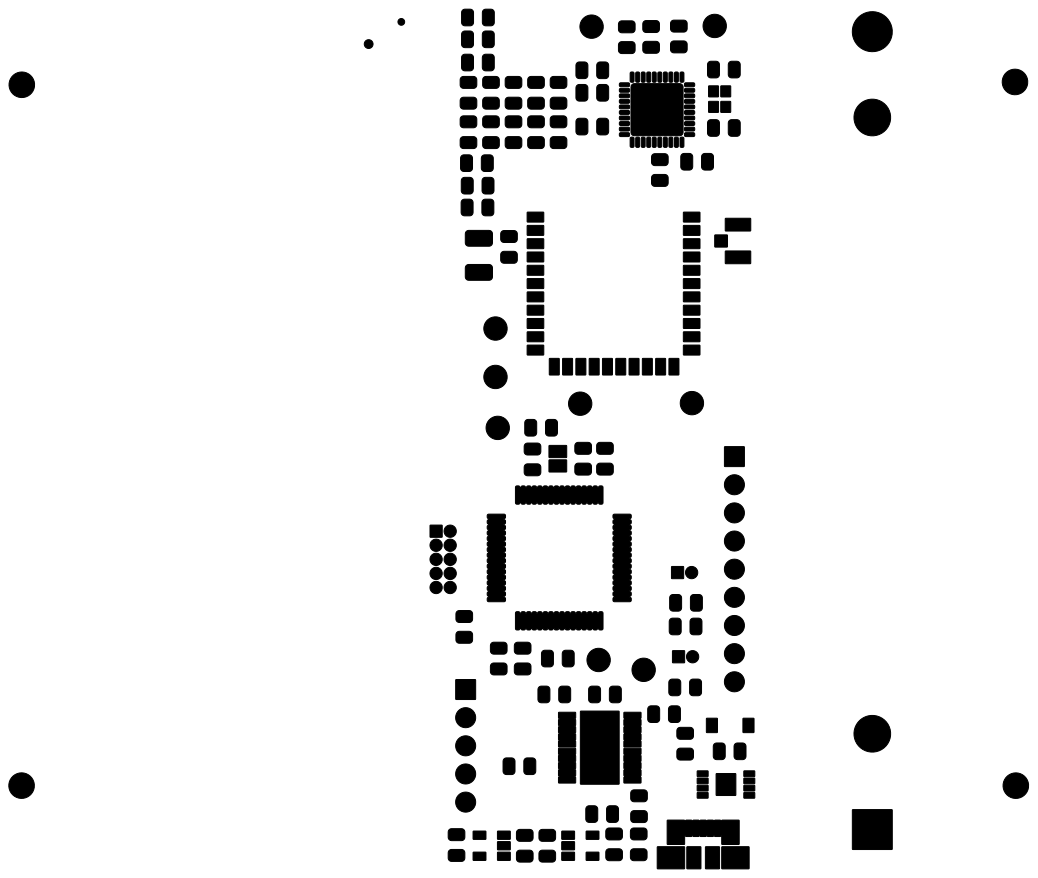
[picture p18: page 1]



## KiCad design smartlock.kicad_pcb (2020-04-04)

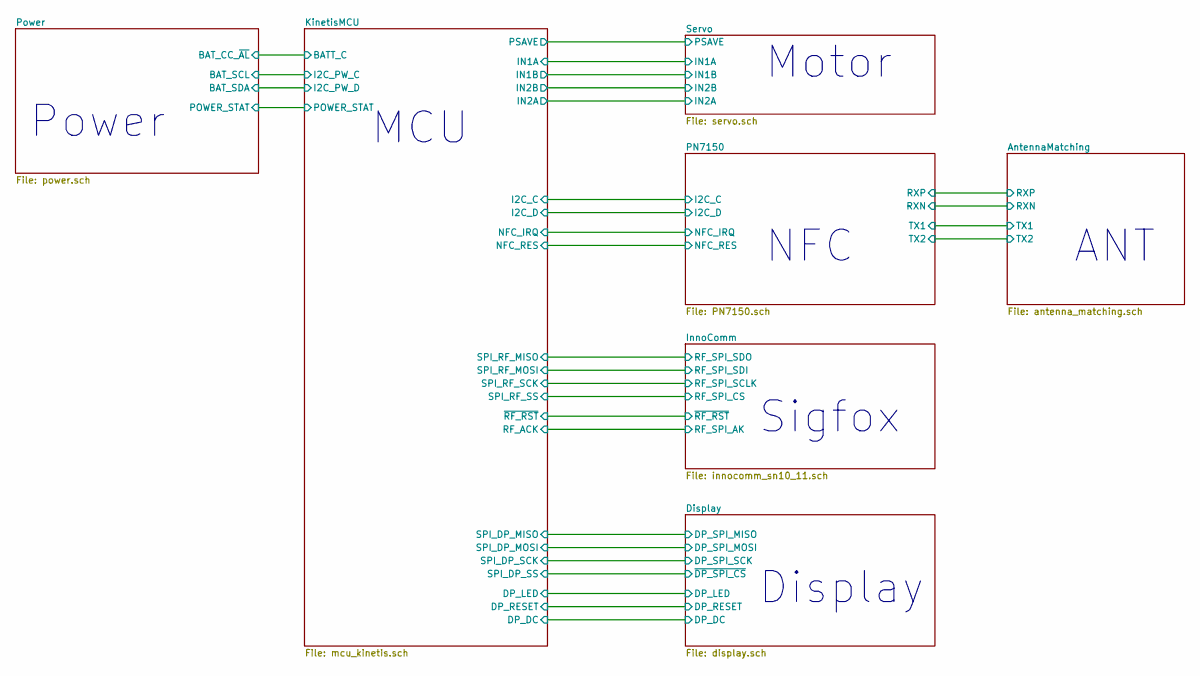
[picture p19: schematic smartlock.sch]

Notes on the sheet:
NFC
ANT
Sigfox
MCU
Power
Display
Motor

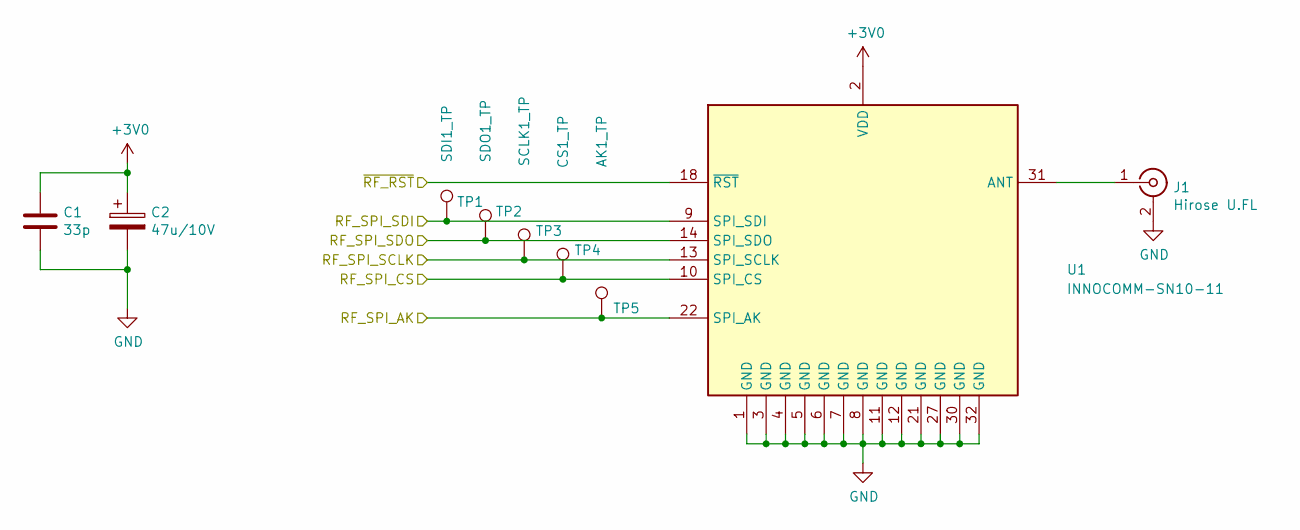
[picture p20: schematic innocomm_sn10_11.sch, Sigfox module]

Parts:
C1: 33p; C_0805_2012Metric
C2: 47u/10V; CP_EIA-3528-21_Kemet-B
J1: Hirose U.FL; U.FL_Hirose_U.FL-R-SMT-1_Vertical
TP1: SDI1_TP; TestPoint_Loop_D2.50mm_Drill1.0mm_LowProfile
TP2: SDO1_TP; TestPoint_Loop_D2.50mm_Drill1.0mm_LowProfile
TP3: SCLK1_TP; TestPoint_Loop_D2.50mm_Drill1.0mm_LowProfile
TP4: CS1_TP; TestPoint_Loop_D2.50mm_Drill1.0mm_LowProfile
TP5: AK1_TP; TestPoint_Loop_D2.50mm_Drill1.0mm_LowProfile
U1: INNOCOMM-SN10-11; InnoCommSN10-11

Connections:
+3V0: C1.1, C2.1, U1.2 (VDD); also elsewhere on the board
/InnoComm/RF_SPI_CS: TP4.1, U1.10 (SPI_CS); also elsewhere on the board
/InnoComm/RF_SPI_SCLK: TP3.1, U1.13 (SPI_SCLK); also elsewhere on the board
/InnoComm/RF_SPI_SDI: TP1.1, U1.9 (SPI_SDI); also elsewhere on the board
/InnoComm/RF_SPI_SDO: TP2.1, U1.14 (SPI_SDO); also elsewhere on the board
/InnoComm/~RF_RST: U1.18 (~RST); also elsewhere on the board
/KinetisMCU/RF_ACK: TP5.1, U1.22 (SPI_AK); also elsewhere on the board
GND: C1.2, C2.2, J1.2 (Ext), U1.1 (GND), U1.3 (GND), U1.4 (GND), U1.5 (GND), U1.6 (GND), U1.7 (GND), U1.8 (GND), U1.11 (GND), U1.12 (GND), U1.21 (GND), U1.27 (GND), U1.30 (GND), U1.32 (GND); also elsewhere on the board
unnamed: J1.1 (In), U1.31 (ANT)

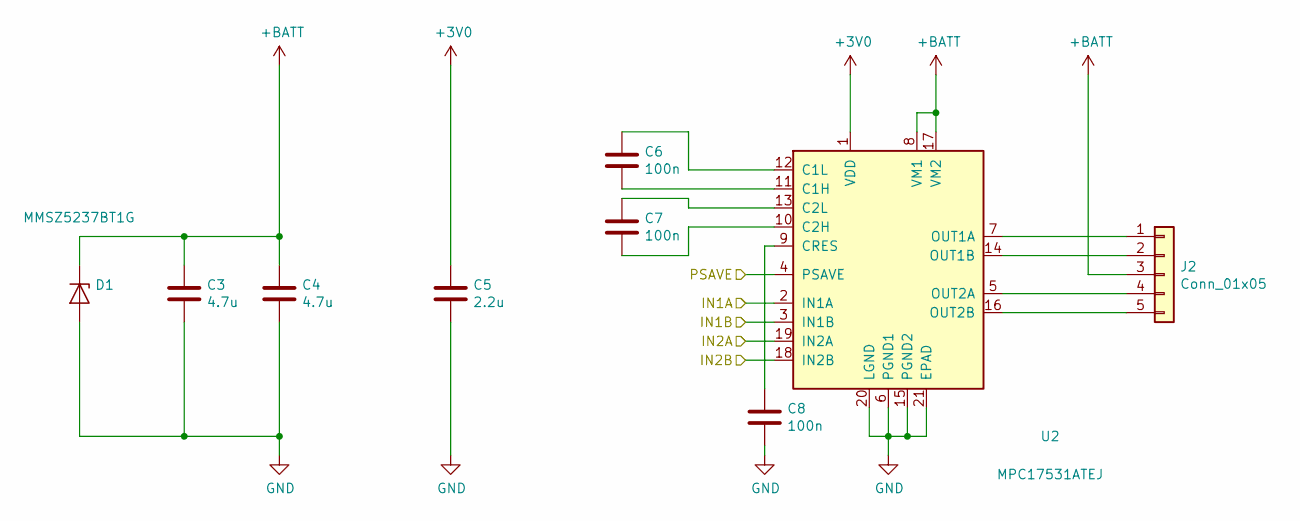
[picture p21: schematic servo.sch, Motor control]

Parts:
C3, C4: 4.7u; C_0805_2012Metric
C5: 2.2u; C_0805_2012Metric
C6, C7, C8: 100n; C_0805_2012Metric
D1: MMSZ5237BT1G; D_SOD-123
J2: Conn_01x05; PinHeader_1x05_P2.54mm_Vertical
U2: MPC17531ATEJ; HTSSOP-20-1EP_4.4x6.5mm_P0.65mm_EP3.4x6.5mm_ThermalVias

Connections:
+3V0: C5.1, U2.1 (VDD); also elsewhere on the board
+BATT: C3.1, C4.1, D1.1 (K), J2.3, U2.8 (VM1), U2.17 (VM2); also elsewhere on the board
/KinetisMCU/IN1A: U2.2 (IN1A); also elsewhere on the board
/KinetisMCU/IN1B: U2.3 (IN1B); also elsewhere on the board
/KinetisMCU/IN2A: U2.19 (IN2A); also elsewhere on the board
/KinetisMCU/IN2B: U2.18 (IN2B); also elsewhere on the board
/KinetisMCU/PSAVE: U2.4 (PSAVE); also elsewhere on the board
GND: C3.2, C4.2, C5.2, C8.2, D1.2 (A), U2.6 (PGND1), U2.15 (PGND2), U2.20 (LGND), U2.21 (EPAD); also elsewhere on the board
unnamed: C6.1, U2.12 (C1L)
unnamed: C6.2, U2.11 (C1H)
unnamed: C7.1, U2.13 (C2L)
unnamed: C7.2, U2.10 (C2H)
unnamed: C8.1, U2.9 (CRES)
unnamed: J2.1, U2.7 (OUT1A)
unnamed: J2.2, U2.14 (OUT1B)
unnamed: J2.4, U2.5 (OUT2A)
unnamed: J2.5, U2.16 (OUT2B)

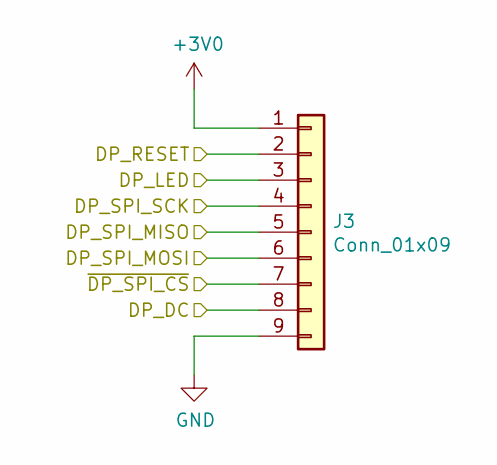
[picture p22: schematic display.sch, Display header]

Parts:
J3: Conn_01x09; PinHeader_1x09_P2.54mm_Vertical

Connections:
+3V0: J3.1; also elsewhere on the board
/Display/DP_DC: J3.8; also elsewhere on the board
/Display/DP_LED: J3.3; also elsewhere on the board
/Display/DP_RESET: J3.2; also elsewhere on the board
/Display/DP_SPI_MISO: J3.5; also elsewhere on the board
/Display/DP_SPI_MOSI: J3.6; also elsewhere on the board
/Display/DP_SPI_SCK: J3.4; also elsewhere on the board
/KinetisMCU/SPI_DP_SS: J3.7; also elsewhere on the board
GND: J3.9; also elsewhere on the board

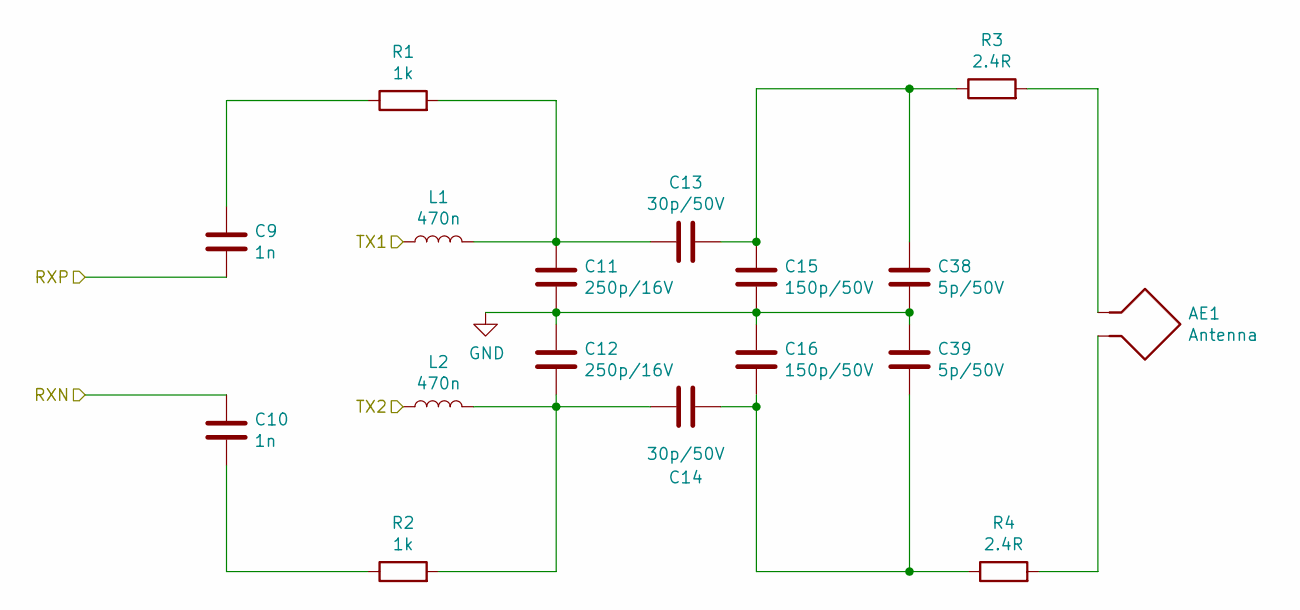
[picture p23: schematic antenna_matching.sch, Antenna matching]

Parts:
AE1: Antenna; nfc_40_75
C9, C10: 1n; C_0805_2012Metric
C11, C12: 250p/16V; C_0805_2012Metric
C13, C14: 30p/50V; C_0805_2012Metric
C15, C16: 150p/50V; C_0805_2012Metric
C38, C39: 5p/50V; C_0805_2012Metric
L1, L2: 470n; L_0805_2012Metric
R1, R2: 1k; R_0805_2012Metric
R3, R4: 2.4R; R_0805_2012Metric

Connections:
/AntennaMatching/RXN: C10.1; also elsewhere on the board
/AntennaMatching/RXP: C9.2; also elsewhere on the board
/AntennaMatching/TX1: L1.1; also elsewhere on the board
/AntennaMatching/TX2: L2.1; also elsewhere on the board
GND: C11.2, C12.1, C15.2, C16.1, C38.2, C39.1; also elsewhere on the board
unnamed: AE1.1, R3.2
unnamed: AE1.2, R4.2
unnamed: C9.1, R1.1
unnamed: C10.2, R2.1
unnamed: C11.1, C13.1, L1.2, R1.2
unnamed: C12.2, C14.1, L2.2, R2.2
unnamed: C13.2, C15.1, C38.1, R3.1
unnamed: C14.2, C16.2, C39.2, R4.1

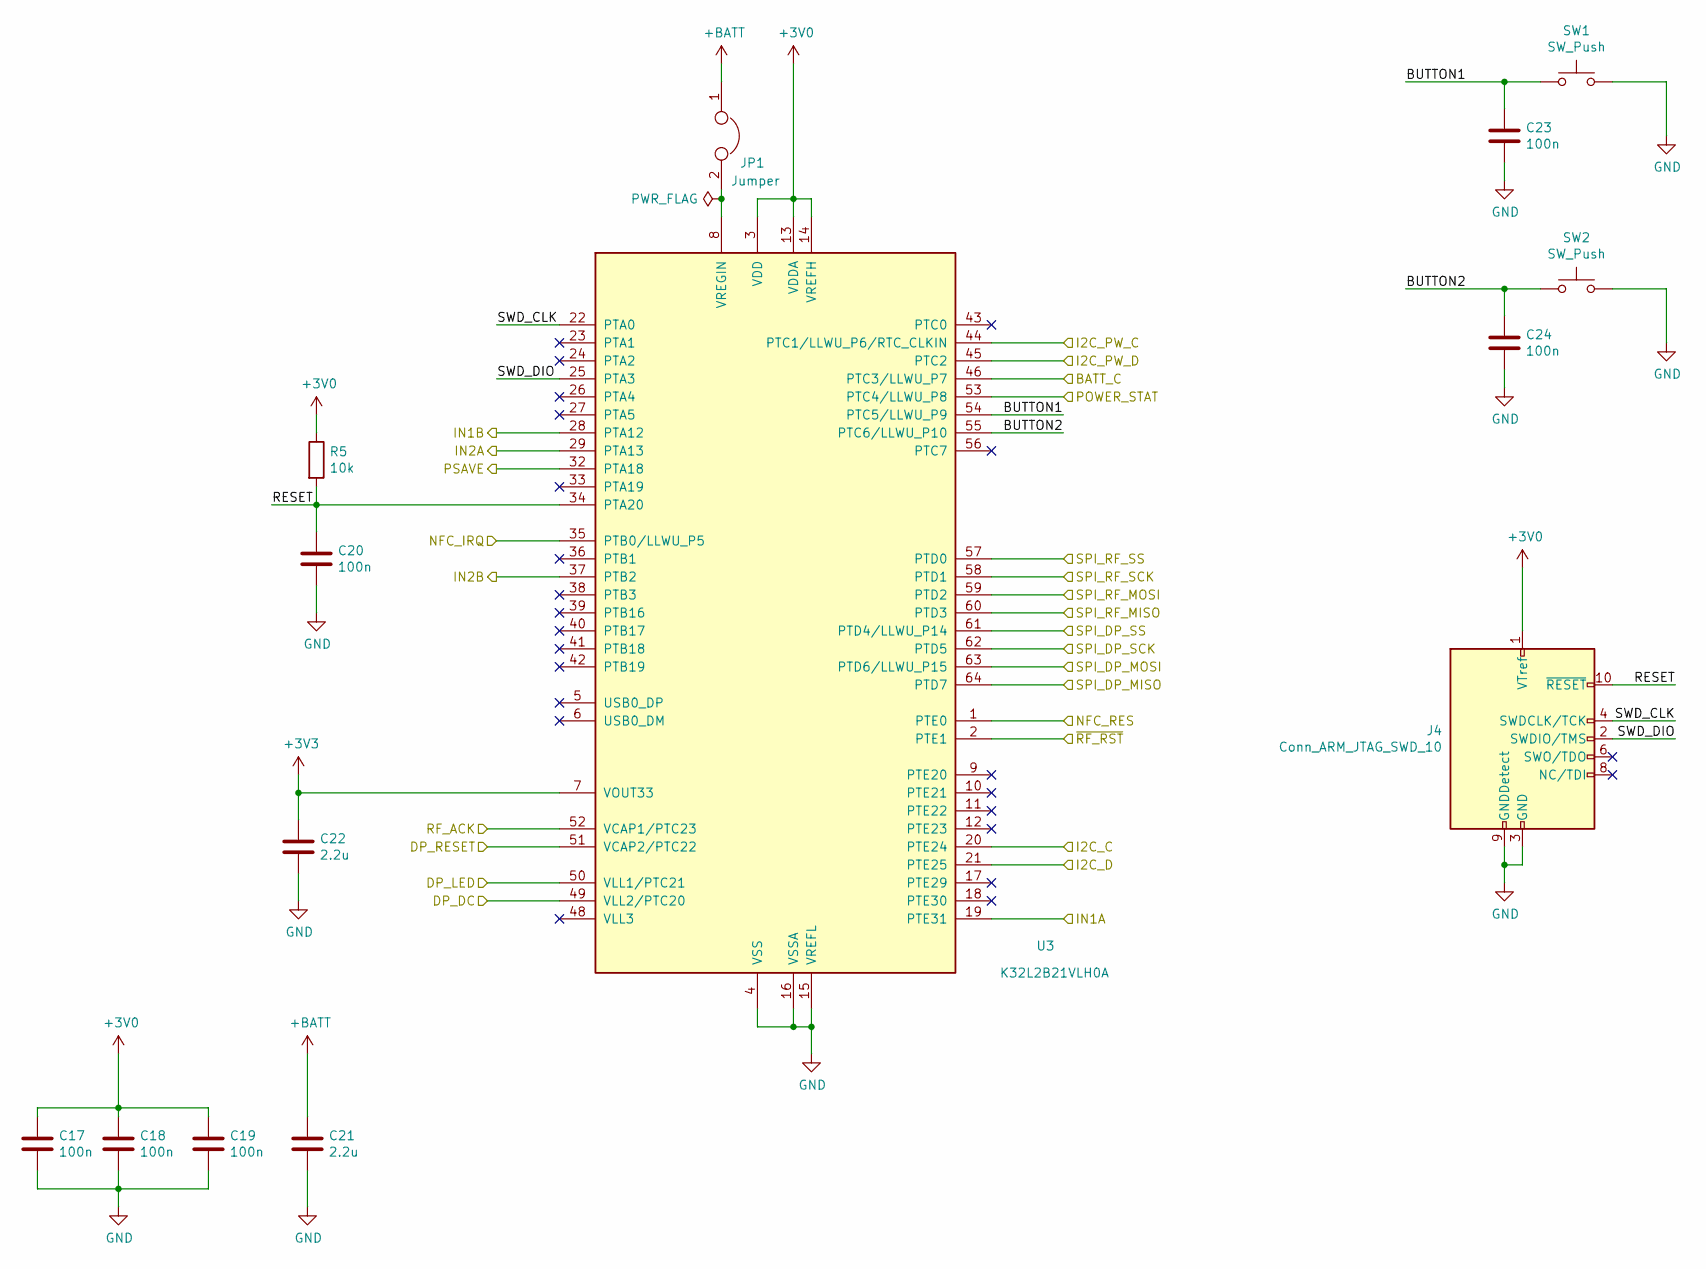
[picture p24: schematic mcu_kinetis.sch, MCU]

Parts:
C17, C18, C19, C20, C23, C24: 100n; C_0805_2012Metric
C21, C22: 2.2u; C_0805_2012Metric
J4: Conn_ARM_JTAG_SWD_10; PinHeader_2x05_P1.27mm_Vertical
JP1: Jumper; SolderJumper-2_P1.3mm_Bridged_Pad1.0x1.5mm
R5: 10k; R_0805_2012Metric
SW1, SW2: SW_Push; PinHeader_1x02_P1.27mm_Vertical
U3: K32L2B21VLH0A; LQFP-64_10x10mm_P0.5mm

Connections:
+3V0: C17.1, C18.1, C19.1, J4.1 (VTref), R5.1, U3.3 (VDD), U3.13 (VDDA), U3.14 (VREFH), U3.30 (VDD); also elsewhere on the board
+3V3: C22.1, U3.7 (VOUT33)
+BATT: C21.1, JP1.1; also elsewhere on the board
/Display/DP_DC: U3.49 (VLL2/PTC20); also elsewhere on the board
/Display/DP_LED: U3.50 (VLL1/PTC21); also elsewhere on the board
/Display/DP_RESET: U3.51 (VCAP2/PTC22); also elsewhere on the board
/Display/DP_SPI_MISO: U3.64 (PTD7); also elsewhere on the board
/Display/DP_SPI_MOSI: U3.63 (PTD6/LLWU_P15); also elsewhere on the board
/Display/DP_SPI_SCK: U3.62 (PTD5); also elsewhere on the board
/InnoComm/RF_SPI_CS: U3.57 (PTD0); also elsewhere on the board
/InnoComm/RF_SPI_SCLK: U3.58 (PTD1); also elsewhere on the board
/InnoComm/RF_SPI_SDI: U3.59 (PTD2); also elsewhere on the board
/InnoComm/RF_SPI_SDO: U3.60 (PTD3); also elsewhere on the board
/InnoComm/~RF_RST: U3.2 (PTE1); also elsewhere on the board
/KinetisMCU/BATT_C: U3.46 (PTC3/LLWU_P7); also elsewhere on the board
/KinetisMCU/BUTTON1: C23.1, SW1.1, U3.54 (PTC5/LLWU_P9)
/KinetisMCU/BUTTON2: C24.1, SW2.1, U3.55 (PTC6/LLWU_P10)
/KinetisMCU/I2C_C: U3.20 (PTE24); also elsewhere on the board
/KinetisMCU/I2C_D: U3.21 (PTE25); also elsewhere on the board
/KinetisMCU/IN1A: U3.19 (PTE31); also elsewhere on the board
/KinetisMCU/IN1B: U3.28 (PTA12); also elsewhere on the board
/KinetisMCU/IN2A: U3.29 (PTA13); also elsewhere on the board
/KinetisMCU/IN2B: U3.37 (PTB2); also elsewhere on the board
/KinetisMCU/NFC_IRQ: U3.35 (PTB0/LLWU_P5); also elsewhere on the board
/KinetisMCU/NFC_RES: U3.1 (PTE0); also elsewhere on the board
/KinetisMCU/POWER_STAT: U3.53 (PTC4/LLWU_P8); also elsewhere on the board
/KinetisMCU/PSAVE: U3.32 (PTA18); also elsewhere on the board
/KinetisMCU/RESET: C20.1, J4.10 (~RESET~), R5.2, U3.34 (PTA20)
/KinetisMCU/RF_ACK: U3.52 (VCAP1/PTC23); also elsewhere on the board
/KinetisMCU/SPI_DP_SS: U3.61 (PTD4/LLWU_P14); also elsewhere on the board
/KinetisMCU/SWD_CLK: J4.4 (SWDCLK/TCK), U3.22 (PTA0)
/KinetisMCU/SWD_DIO: J4.2 (SWDIO/TMS), U3.25 (PTA3)
/Power/BAT_SCL: U3.44 (PTC1/LLWU_P6/RTC_CLKIN); also elsewhere on the board
/Power/BAT_SDA: U3.45 (PTC2); also elsewhere on the board
GND: C17.2, C18.2, C19.2, C20.2, C21.2, C22.2, C23.2, C24.2, J4.3 (GND), J4.5 (GND), J4.9 (GNDDetect), SW1.2, SW2.2, U3.4 (VSS), U3.15 (VREFL), U3.16 (VSSA), U3.31 (VSS), U3.47 (VSS); also elsewhere on the board
unnamed: JP1.2, U3.8 (VREGIN)

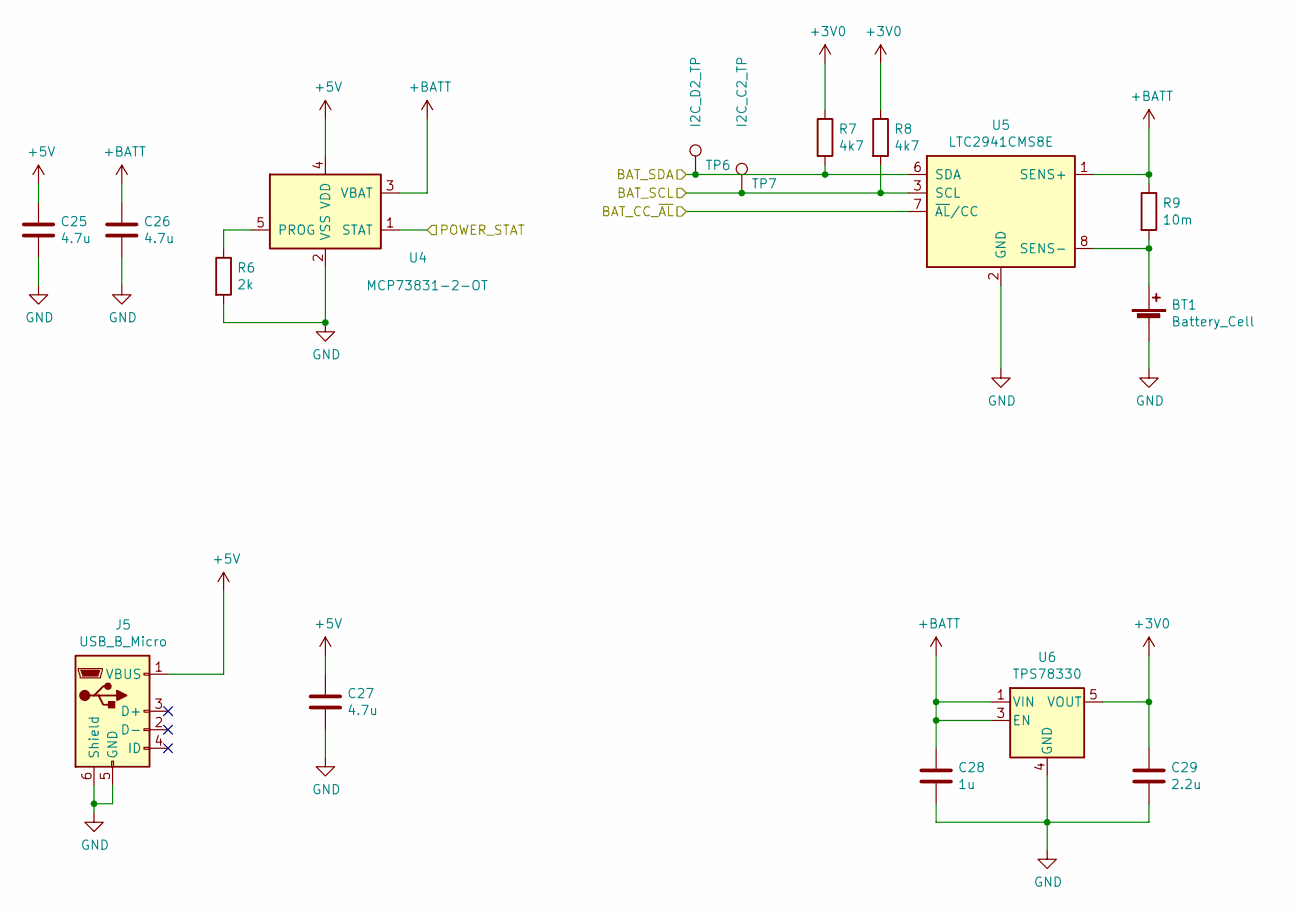
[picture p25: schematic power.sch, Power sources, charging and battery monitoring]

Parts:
BT1: Battery_Cell; BatteryHolder_MPD_BH-18650-PC2
C25, C26, C27: 4.7u; C_0805_2012Metric
C28: 1u; C_0805_2012Metric
C29: 2.2u; C_0805_2012Metric
J5: USB_B_Micro; USB_Micro-B_Molex_47346-0001
R6: 2k; R_0805_2012Metric
R7, R8: 4k7; R_0805_2012Metric
R9: 10m; R_0805_2012Metric
TP6: I2C_D2_TP; TestPoint_Loop_D2.50mm_Drill1.0mm_LowProfile
TP7: I2C_C2_TP; TestPoint_Loop_D2.50mm_Drill1.0mm_LowProfile
U4: MCP73831-2-OT; SOT-23-5
U5: LTC2941CMS8E; MSOP-8-1EP_3x3mm_P0.65mm_EP1.68x1.88mm
U6: TPS78330; SOT-23-5

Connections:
+3V0: C29.1, R7.1, R8.1, U6.5 (VOUT); also elsewhere on the board
+5V: C25.1, C27.1, J5.1 (VBUS), U4.4 (VDD)
+BATT: C26.1, C28.1, R9.1, U4.3 (VBAT), U5.1 (SENS+), U6.1 (VIN), U6.3 (EN); also elsewhere on the board
/KinetisMCU/BATT_C: U5.7 (~AL~/CC); also elsewhere on the board
/KinetisMCU/POWER_STAT: U4.1 (STAT); also elsewhere on the board
/Power/BAT_SCL: R8.2, TP7.1, U5.3 (SCL); also elsewhere on the board
/Power/BAT_SDA: R7.2, TP6.1, U5.6 (SDA); also elsewhere on the board
GND: BT1.2 (-), C25.2, C26.2, C27.2, C28.2, C29.2, J5.5 (GND), J5.6 (Shield), R6.2, U4.2 (VSS), U5.2 (GND), U6.2 (GND), U6.4 (GND); also elsewhere on the board
unnamed: BT1.1 (+), R9.2, U5.8 (SENS-)
unnamed: R6.1, U4.5 (PROG)

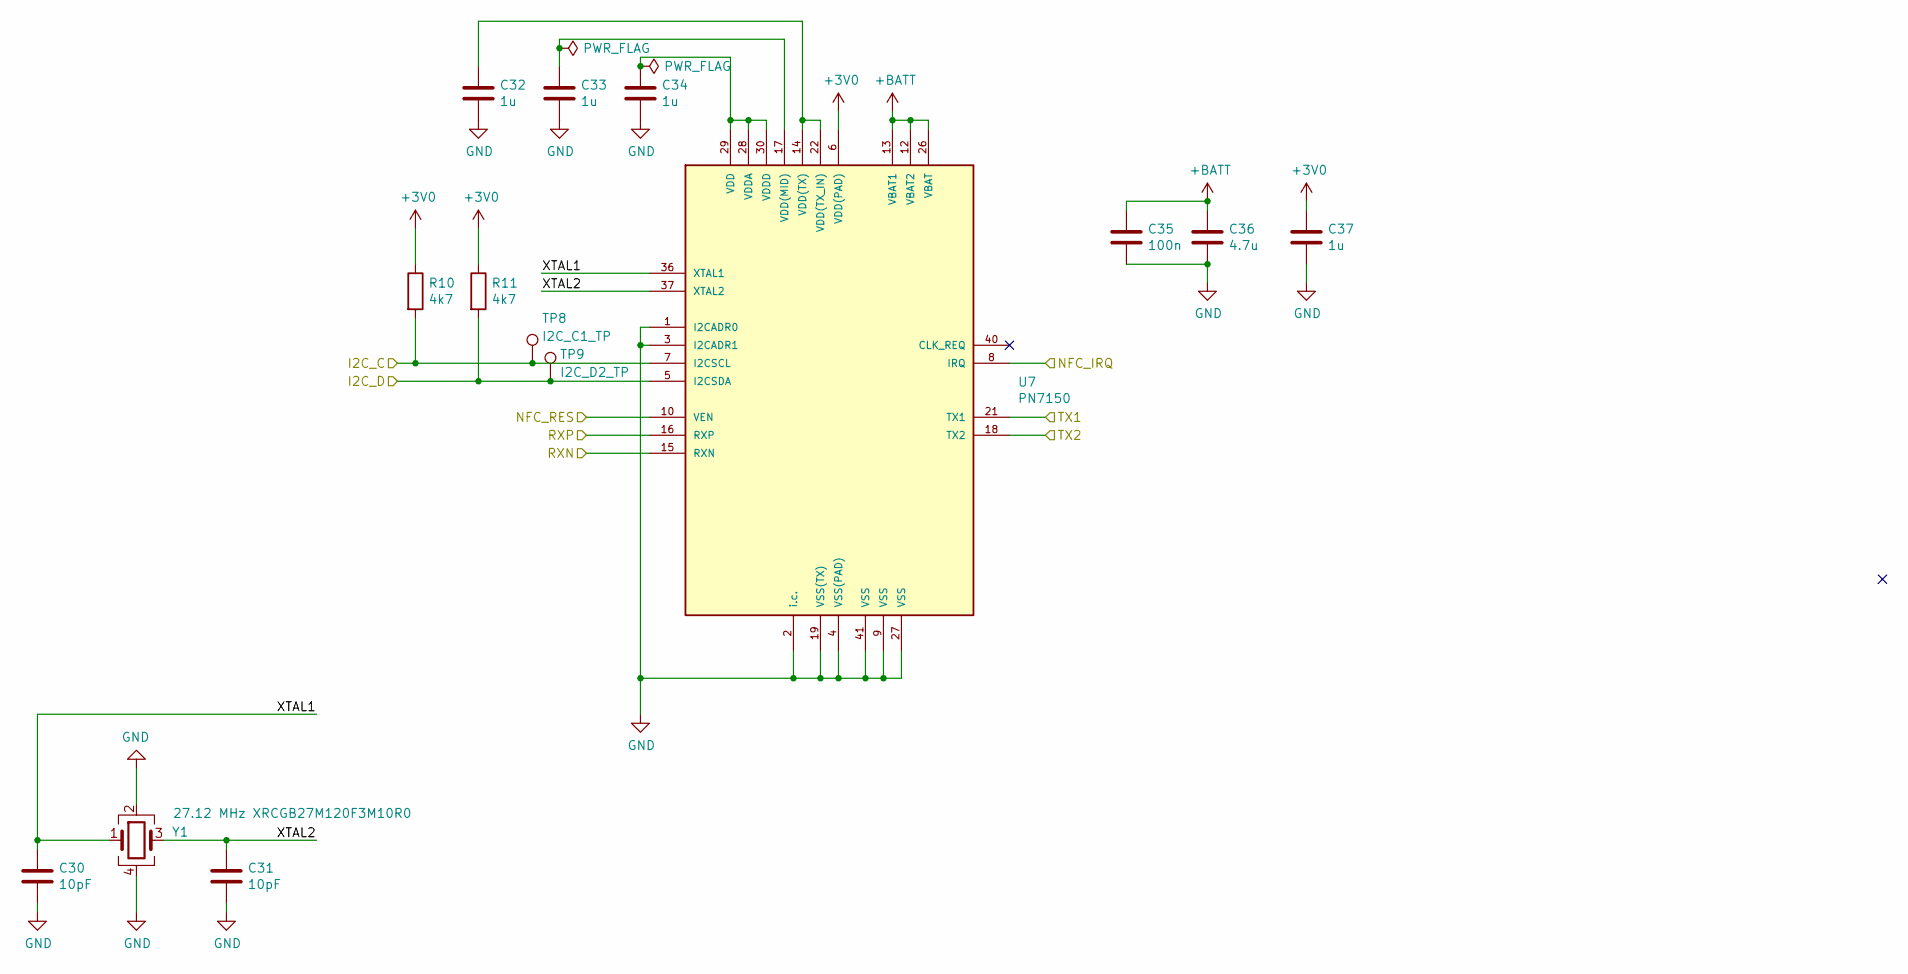
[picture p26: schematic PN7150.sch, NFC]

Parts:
C30, C31: 10pF; C_0805_2012Metric
C32, C33, C34, C37: 1u; C_0805_2012Metric
C35: 100n; C_0805_2012Metric
C36: 4.7u; C_0805_2012Metric
R10, R11: 4k7; R_0805_2012Metric
TP8: I2C_C1_TP; TestPoint_Loop_D2.50mm_Drill1.0mm_LowProfile
TP9: I2C_D2_TP; TestPoint_Loop_D2.50mm_Drill1.0mm_LowProfile
U7: PN7150; QFN-40-1EP_6x6mm_P0.5mm_EP4.6x4.6mm
Y1: 27.12 MHz XRCGB27M120F3M10R0; Crystal_SMD_2016-4Pin_2.0x1.6mm

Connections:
+3V0: C37.1, R10.1, R11.1, U7.6 (VDD(PAD)); also elsewhere on the board
+BATT: C35.1, C36.1, U7.12 (VBAT2), U7.13 (VBAT1), U7.26 (VBAT); also elsewhere on the board
/AntennaMatching/RXN: U7.15 (RXN); also elsewhere on the board
/AntennaMatching/RXP: U7.16 (RXP); also elsewhere on the board
/AntennaMatching/TX1: U7.21 (TX1); also elsewhere on the board
/AntennaMatching/TX2: U7.18 (TX2); also elsewhere on the board
/KinetisMCU/I2C_C: R10.2, TP8.1, U7.7 (I2CSCL); also elsewhere on the board
/KinetisMCU/I2C_D: R11.2, TP9.1, U7.5 (I2CSDA); also elsewhere on the board
/KinetisMCU/NFC_IRQ: U7.8 (IRQ); also elsewhere on the board
/KinetisMCU/NFC_RES: U7.10 (VEN); also elsewhere on the board
/PN7150/XTAL1: C30.1, U7.36 (XTAL1), Y1.1
/PN7150/XTAL2: C31.1, U7.37 (XTAL2), Y1.3
GND: C30.2, C31.2, C32.2, C33.2, C34.2, C35.2, C36.2, C37.2, U7.1 (I2CADR0), U7.2 (i.c.), U7.3 (I2CADR1), U7.4 (VSS(PAD)), U7.9 (VSS), U7.19 (VSS(TX)), U7.27 (VSS), U7.41 (VSS), Y1.2, Y1.4; also elsewhere on the board
unnamed: C32.1, U7.14 (VDD(TX)), U7.22 (VDD(TX_IN))
unnamed: C33.1, U7.17 (VDD(MID))
unnamed: C34.1, U7.28 (VDDA), U7.29 (VDD), U7.30 (VDDD)

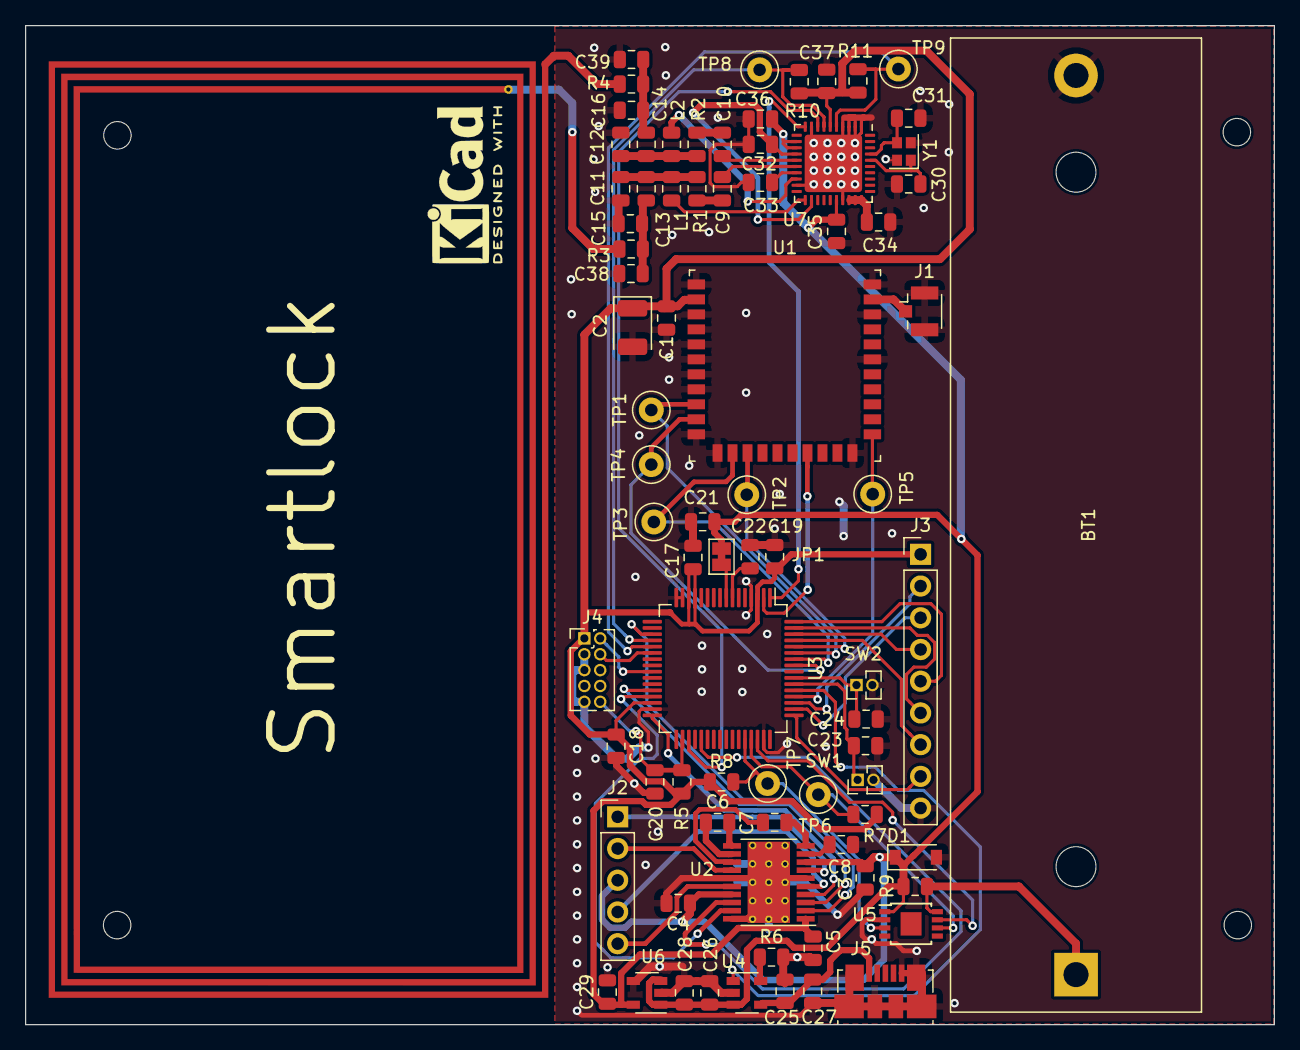
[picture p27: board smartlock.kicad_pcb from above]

Board: 2 copper layers, 100.0 x 80.0 mm, 80 parts (0 on the bottom side), 66 nets.
